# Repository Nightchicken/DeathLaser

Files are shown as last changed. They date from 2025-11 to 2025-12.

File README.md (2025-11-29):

# 🧠 ESP32 Project – ESP32 

## 👥 Team Members
| Name | Role | Contribution Summary |
|---|---|---|
| Bryon Cobb | | [Describe what they did briefly] |
| Matthew Kabat | | [Describe what they did briefly] |
| Joel Bowman | | [Describe what they did briefly] |
| Jett Moericke | | [Describe what they did briefly] |
| Steven Yang | | [Describe what they did briefly] |

1. Camera reading
2. Servo movement and limits
3. Laser on/off
4. Optional web based controller

Design and Fabrication of a Dual-Axis Servo Turret Mounts
Designed & Created by: Joel Bowman

1.	Motivation

The design of a dual-axis turret serves as a practical demonstration of the ESP-32 microcontroller’s capabilities. Although the ESP-32 is based on a RISC architecture with a reduced instruction set, it remains highly capable of generating precise pulse-width modulation (PWM) signals required for servo control. By integrating two MG995 servos, the system achieves motion along both the X and Y axes, enabling accurate positioning and tracking. When equipped with a camera, the turret can collect visual data and execute real-time tracking operations, showcasing the ESP-32’s ability to coordinate hardware and software tasks. This project therefore highlights not only the mechanical design and fabrication of servo mounts, but also the broader technical achievement of combining embedded control, signal modulation, and data-driven actuation in a cohesive system.
2.	Objectives

1.	To design, fabricate, and test servo brackets for MG995 servos enabling dual-axis rotation.          
2.	Mounts must securely hold the MG995 servos. 
3.	High strength is required to hold the weight extra attachments (Not breaking under use). 

3. Design Methodology and Materials 
•	CAD Modeling:
o	Tools used: Tinker CAD.
o	Designed plan: Breaking down the 
 
•	3D Printer Filament Material Selection:
o	PETG is chosen for durability, flexibility, and heat resistance compared to PLA.
o	While PETG is not as durable as TPU it is more ridged and easier to manufacture making it ideal material for mounting hardware.
o	PETG brand used and Specs:

4. Fabrication Process
3D Printing Setup
•	Printer Model: Creality Ender V3 SE
 
•	Nozzle Diameter: 0.2 mm
•	Layer Height: 0.2 mm
•	Infill Density: 45% (grid pattern)
•	Print Speed: 45 mm/s (optimized for PETG)
•	Material: PETG filament, selected for its higher impact resistance and thermal stability compared to PLA.
Observed Challenges:
•	PETG stringing due to insufficient retraction settings.
•	Bed adhesion difficulties requiring surface treatment.
•	Warping at bracket edges under prolonged print cycles.
•	Poor interlayer bonding at higher print speeds.
Assembly
•	Servo Mounting: MG995 servos were secured into the printed brackets using mechanical fasteners.
•	Fasteners: 1.4 × 12 mm screws, selected to reduce stress concentration and allow thicker bracket walls compared to larger bolts.
•	Wiring: Standard jumper wires were used for prototyping, enabling rapid connection to the ESP-32 microcontroller.
5. System Integration
The turret employs a dual-axis configuration:
•	Bottom Servo (Yaw): Provides rotation along the X-axis.
•	Top Servo (Pitch): Mounted orthogonally to enable vertical rotation along the Y-axis.
Control Architecture:
•	The ESP-32 generates PWM signals to modulate servo position.
•	Signals are routed through the servo driver circuitry.
•	Mechanical motion is achieved via the coupled servo brackets.

6. Challenges Encountered
•	Bracket Dimensions and Fitment: Initial bracket iterations obstructed servo insertion due to interference with structural features. Other designs were too thin, resulting in cracking under load when using 4 × 12 mm bolts. Transitioning to 1.4 × 12 mm screws allowed thicker bracket walls and improved rigidity.
o	Solution: Increased infill to 100% and introduced pilot holes using a 1/64 in drill bit. Simplified bracket geometry reduced stress concentrations and improved both print quality and mechanical strength.
•	Layer Adhesion in PETG: PETG requires precise tuning to achieve strong interlayer bonding. At default slicer settings (70 mm/s), adhesion was poor, leading to fragile parts.
o	Solution: Research indicated optimal print speeds between 35–50 mm/s. Adjusting to 40 mm/s improved layer fusion and overall part durability without sacrificing print time efficiency.
Minor Printing Issues
•	Bed Adhesion: Improved using glue stick application and elevated bed temperatures.
•	Stringing: Mitigated through retraction tuning and nozzle temperature adjustments.
Mechanical Issues
•	Bracket Snapping: Occurred under torque loads with larger bolts. Switching to smaller screws reduced localized stress and enabled thicker bracket design.
•	Reinforcement Strategies: Implemented 8 perimeter wall loops and increased infill density to enhance load-bearing capacity.
7. Results & Testing
•	Turret Performance:
o	Range of motion achieved.
o	Stability underload.
o	No misalignments and major vibrations.
 
8. Conclusion
	Overall, the task was a success as the Ender V3 SE performed well. Showing that Knowledge about the material and tunning was the most important aspect. As most of the issues occurring were due to improper tunning or a design that was not optimal for the structural limitations of the PETG. 
9. References/Specs 

---

## 🧩 1. Project Overview
Briefly describe your ESP32 project — Our group has used an Esp-32 to monitor heat signatures with a Thermal camera and upon finding an acceptable targert moving multiple lazer pointer to engage the target

---

## 🧱 2. Block Diagram
Provide a high-level **block diagram** showing the system components and their interactions.

**Example Layout:**

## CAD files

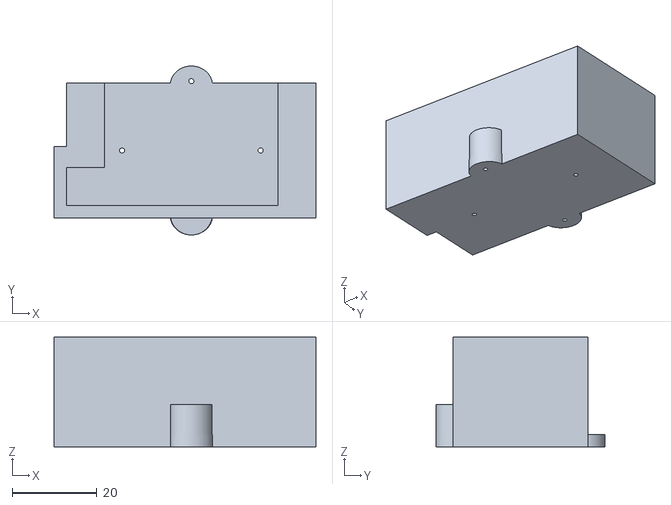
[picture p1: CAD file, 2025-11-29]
STL_Files/Top_servo_Mount_v8.stl
62.0 x 40.0 x 26.0

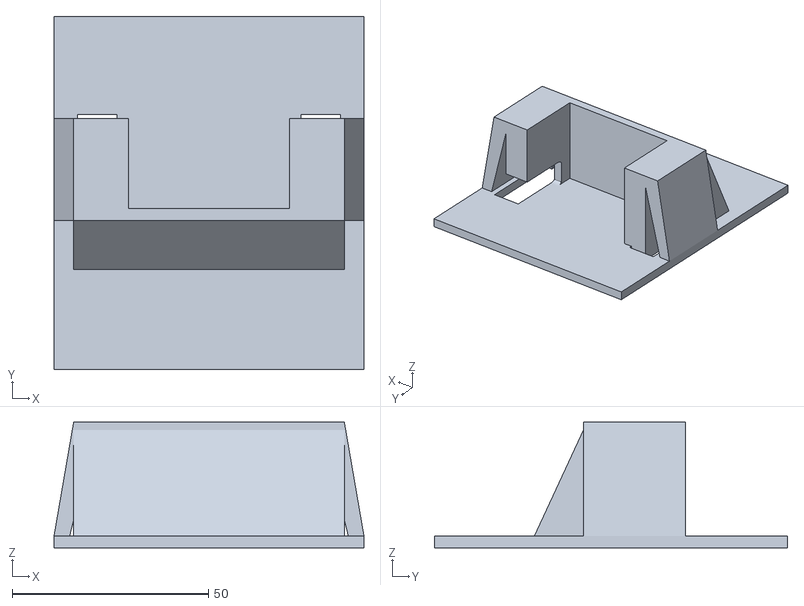
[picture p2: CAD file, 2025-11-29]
STL_Files/Turret Base V5 (1).stl
79.0 x 90.0 x 32.0

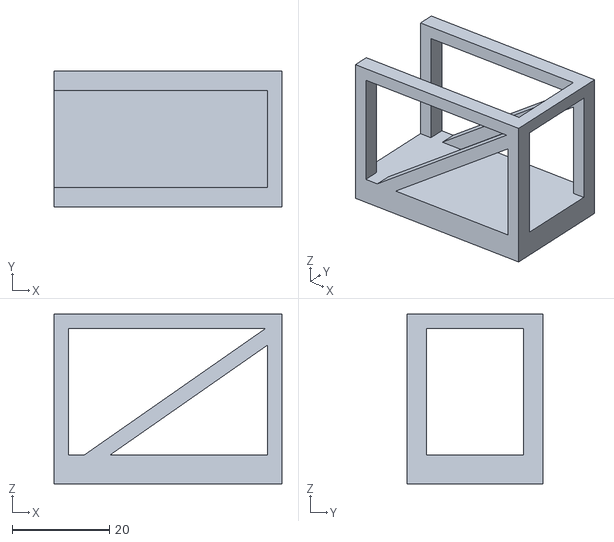
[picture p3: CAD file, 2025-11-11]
STL_Files/Turret Base V2-Skeleton.stl
47.0 x 28.0 x 35.0

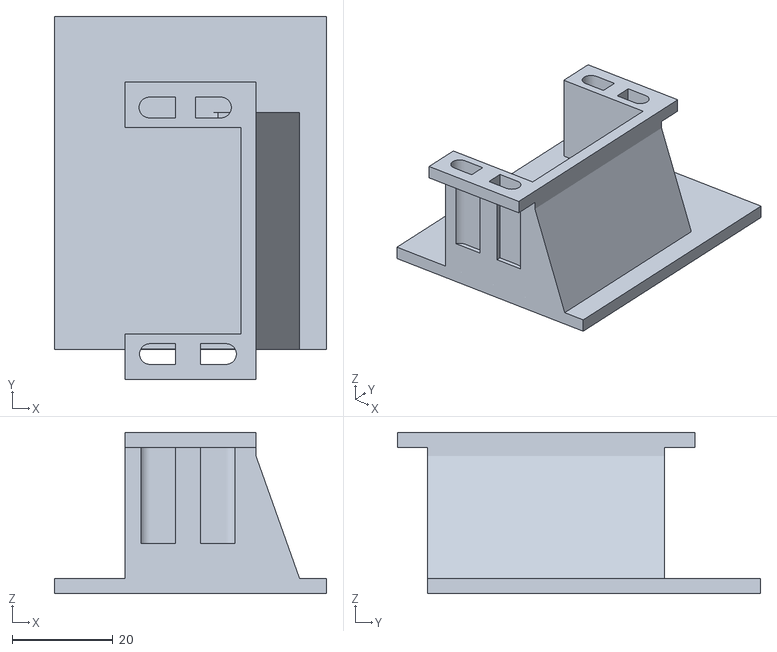
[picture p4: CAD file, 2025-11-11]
STL_Files/Turret Base V4.stl
54.0 x 72.0 x 32.0

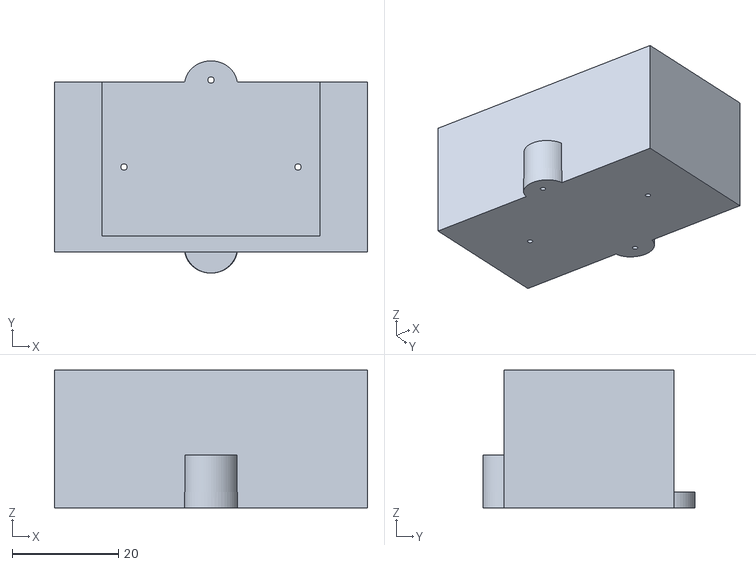
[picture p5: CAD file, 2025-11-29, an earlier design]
STL_Files/Top_servo_Mount_v7.stl
59.0 x 40.0 x 26.0

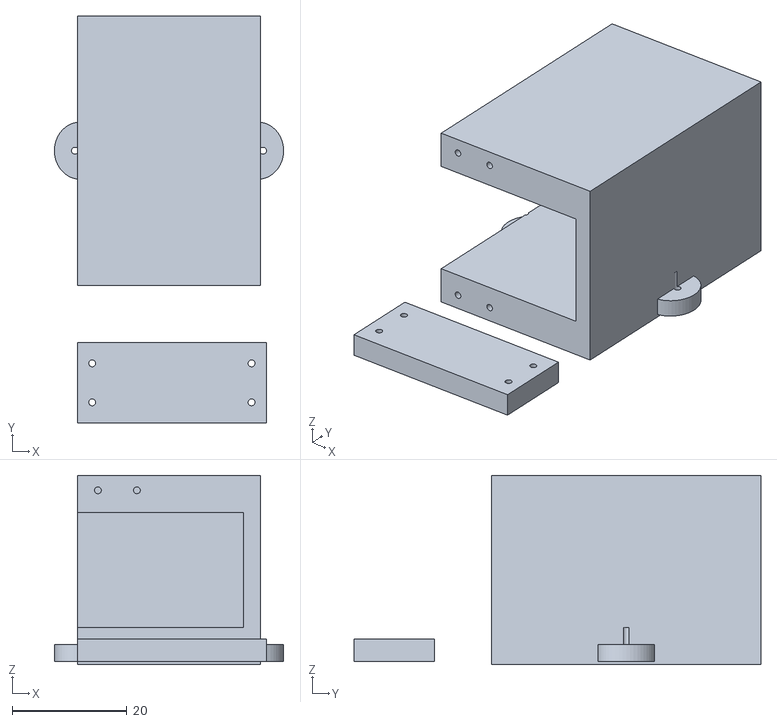
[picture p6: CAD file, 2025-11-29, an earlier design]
STL_Files/Top_servo_Mount_v6_5.stl
40.0 x 71.0 x 33.0

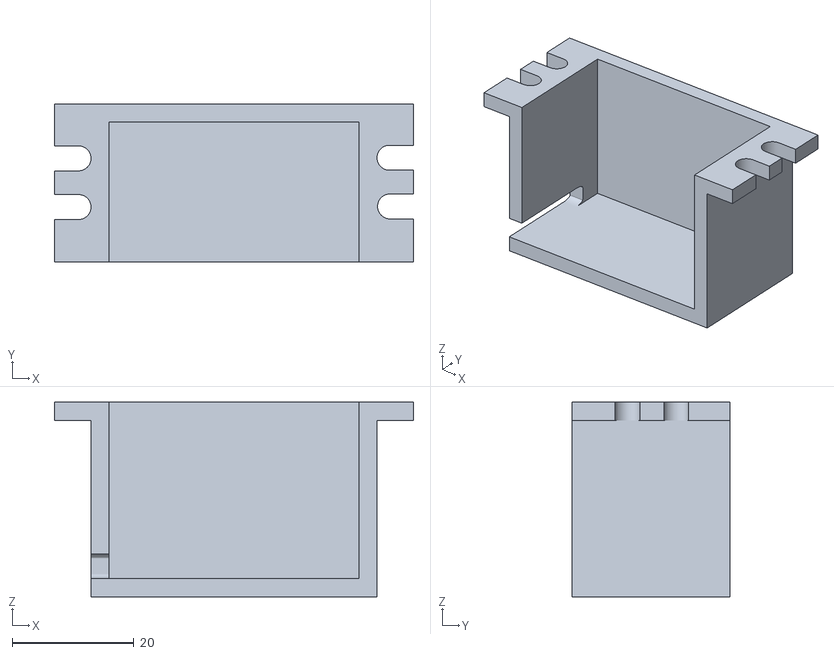
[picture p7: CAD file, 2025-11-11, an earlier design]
STL_Files/Turret Base V2_5.stl
59.0 x 26.0 x 32.0

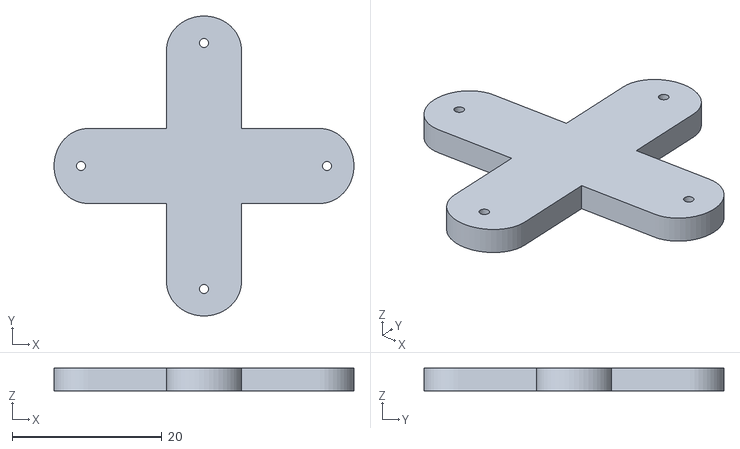
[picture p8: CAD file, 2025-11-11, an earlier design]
STL_Files/Top_servo_Mount_v1.stl
40.0 x 40.0 x 3.00

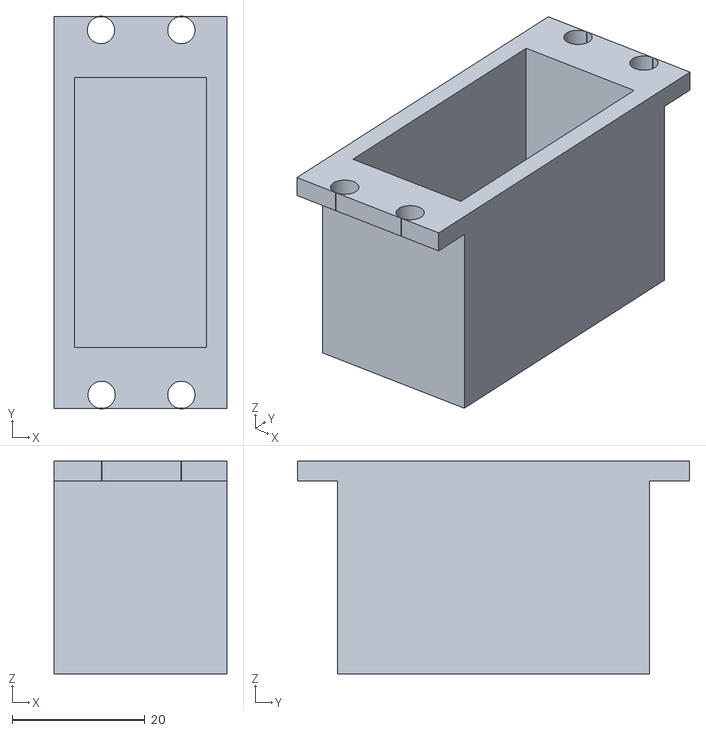
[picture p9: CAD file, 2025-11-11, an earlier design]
STL_Files/Turret Base V1.stl
26.0 x 59.0 x 32.0

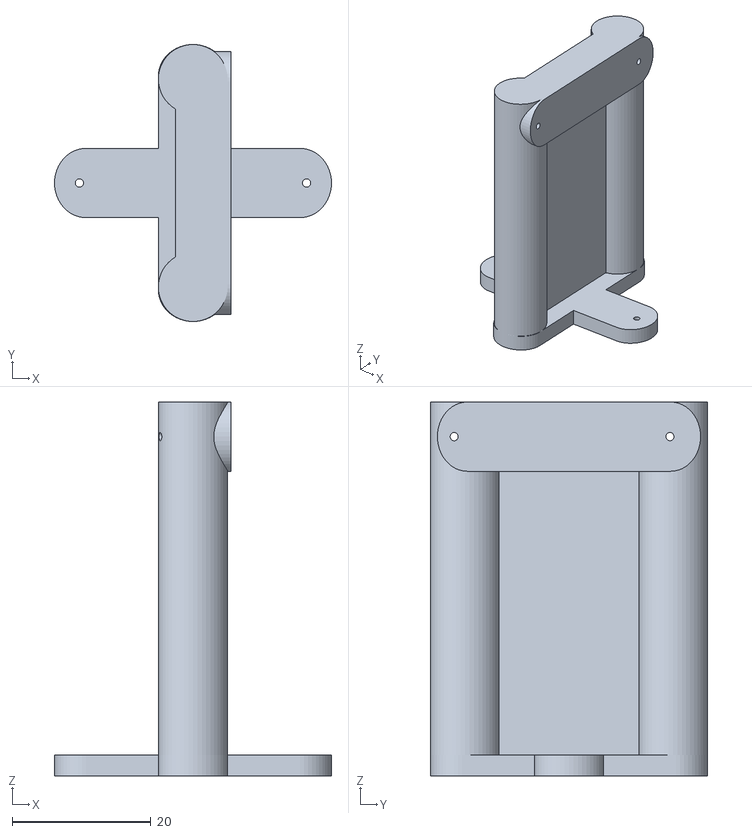
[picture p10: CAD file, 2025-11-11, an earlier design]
STL_Files/Top_servo_Mount_v2.stl
40.0 x 40.0 x 54.0

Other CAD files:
STL_Files/Turret Base V3.stl

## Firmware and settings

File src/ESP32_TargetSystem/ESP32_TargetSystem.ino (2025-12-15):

#include <Arduino.h>
#include "SystemInit.h"
#include "CameraController.h"
#include "LaserController.h"
#include "StorageManager.h"
#include "Patrol.h"

// ================================================================
// CONFIGURATION
// ================================================================
const int PAN_SERVO_PIN  = 25;
const int TILT_SERVO_PIN = 26;
const int SERIAL_BAUD    = 115200;

// ================================================================
// GLOBAL OBJECTS
// ================================================================
Patrol            patrol;            // Handles servo movement and pausing
LaserController   laserController;   // Handles laser firing logic
CameraController* cameraController = nullptr; // Singleton pointer
StorageManager* storageManager   = nullptr; // Singleton pointer

// ================================================================
// SETUP
// ================================================================
void setup() {
  // 1. Basic System Init
  SystemInit::beginSerial(SERIAL_BAUD);
  SystemInit::printBanner();

  // 2. Initialize Storage Singleton
  storageManager = StorageManager::getInstance();
  if (!storageManager->begin()) {
    Serial.println("[Error] SD Card failed or missing.");
  } else {
    storageManager->logEvent("System boot started.");
  }

  // 3. Initialize Patrol System
  // This automatically attaches servos and moves them to start position
  patrol.begin(PAN_SERVO_PIN, TILT_SERVO_PIN);
  Serial.println("[System] Patrol initialized.");

  // 4. Initialize Power & GPIO
  SystemInit::initGPIO();
  SystemInit::initCameraPower();

  // 5. Initialize Camera Singleton
  cameraController = CameraController::getInstance();
  if (!cameraController) {
    Serial.println("[CRITICAL] CameraController returned null!");
  }

  // 6. Initialize Laser Controller
  if (!laserController.begin()) {
    Serial.println("[Error] Laser controller init failed.");
  }

  if (storageManager) storageManager->logEvent("System setup complete.");
}

// ================================================================
// LOOP
// ================================================================
void loop() {
  // 1. UPDATE PATROL
  // This manages the servo movement AND the 5-second internal timer.
  patrol.update();

  // 2. CHECK LOCK STATE
  // If the patrol is "locked" (paused because we saw a target), 
  // we skip detection and just keep the signal active.
  if (patrol.isLocked()) {
    // Keep the laser ON to signal "I saw something"
    laserController.fireLaser(true); 
    
    // Exit loop early. We don't want to detect or save new photos 
    // while we are waiting for the 5-second timer to finish.
    return; 
  }

  // --- If we get here, we are actively searching ---

  // 3. LOOP RATE LIMITER
  // Camera reads are slow (~60ms), so we limit the loop speed to match.
  static unsigned long lastLoopMs = 0;
  unsigned long now = millis();
  if (now - lastLoopMs < 60) {
    return; 
  }
  lastLoopMs = now;

  // Safety Checks
  if (!cameraController || !storageManager) return;

  // 4. DETECT TARGET
  TargetInfo target = cameraController->captureAndDetectTarget(0.0f);
  
  // 5. DECISION LOGIC
  bool hasTarget = (target.confidence > 0.6f);

  if (hasTarget) {
    // --- TARGET ACQUIRED ---
    
    // A. Freeze the patrol (starts the 5-second timer inside Patrol class)
    patrol.onTargetFound();

    // B. Signal Immediately (Laser ON)
    laserController.fireLaser(true); 

    // C. Save Data & Thermal Photo (Happens once per detection event)
    storageManager->saveDetection(target.x, target.y, target.confidence);
    storageManager->saveThermalFrame(cameraController->getConstFrame(), 768);
    
    // Log it
    String logMsg = "Target Locked. Conf: " + String(target.confidence);
    storageManager->logEvent(logMsg);
    Serial.println(logMsg);

  } else {
    // --- NO TARGET ---
    // Ensure lasers are OFF while searching
    laserController.fireLaser(false);
  }
}

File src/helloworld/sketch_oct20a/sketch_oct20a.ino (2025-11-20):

#include <Arduino.h>
#include <Servo.h>

// ----- Servo Setup -----
Servo servo_bottom;
Servo servo_top;

// ----- Function Declaration -----
void patrol();

void setup() {
  servo_bottom.attach(9, 500, 2500);
  servo_top.attach(8, 500, 2500);

  Serial.begin(9600);
  Serial.println("Starting patrol...");
}

void loop() {
  patrol();
}

// ----- Function Definition -----
void patrol() {
  for (int bottomPos = 0; bottomPos <= 180; bottomPos += 20) {
    servo_bottom.write(bottomPos);
    delay(15);

    for (int topPos = 0; topPos <= 180; topPos++) {
      servo_top.write(topPos);
      delay(10);
    }
  }

  for (int bottomPos = 180; bottomPos >= 0; bottomPos -= 20) {
    servo_bottom.write(bottomPos);
    delay(15);

    for (int topPos = 0; topPos <= 180; topPos++) {
      servo_top.write(topPos);
      delay(10);
    }
  }
}

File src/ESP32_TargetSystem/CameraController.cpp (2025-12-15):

#include "CameraController.h" 
#include <Wire.h> 
#include <memory>
#include <fstream>
#include <Arduino.h> 

// >>>>>> SWITCHED TO ADAFRUIT LIBRARY <<<<<<
#include <Adafruit_MLX90640.h>

// Define the sensor object
static Adafruit_MLX90640 mlx; 

// =================================================================
// 1. STATIC MEMBER INITIALIZATION
// =================================================================
CameraController* CameraController::instancePtr = nullptr; 

// =================================================================
// 2. CONSTRUCTOR AND DESTRUCTOR
// =================================================================
CameraController::CameraController(){
    isConfigured = configureCamera();
    if (!isConfigured) {
        Serial.println("[Camera] Failed to configure camera.");
    } else {
        Serial.println("[Camera] Initialized.");
    }
}

CameraController::~CameraController(){
}

// =================================================================
// 3. SINGLETON GETTER
// =================================================================
CameraController* CameraController::getInstance(){
    if (instancePtr == nullptr){
        instancePtr = new CameraController(); 
    }
    return instancePtr;
}

// =================================================================
// 4. CORE CAMERA METHODS (Updated for Adafruit)
// =================================================================

bool CameraController::configureCamera(){
    // 1. Initialize I2C 
    Wire.begin(); 
    Wire.setClock(1000000); // 1 MHz clock for high FPS
    
    Serial.print("[Camera] Initializing MLX90640 (Adafruit Lib)...");
    
    // 2. Initialize Sensor (Adafruit uses begin() with address and Wire pointer)
    if (!mlx.begin(MLX90640_I2CADDR_DEFAULT, &Wire)) {
        Serial.println("FAILED. Check wiring!");
        isConfigured = false;
        return false;
    }
    
    // 3. Set Refresh Rate (Adafruit uses specific enums)
    mlx.setMode(MLX90640_CHESS); // 'Chess' mode is generally better for accuracy
    mlx.setResolution(MLX90640_ADC_18BIT);
    mlx.setRefreshRate(MLX90640_16_HZ);
    
    Serial.println("SUCCESS.");
    isConfigured = true;
    return true; 
}

float* CameraController::getFrame() {
    if (!isConfigured) {
        Serial.println("[Camera] ERROR: Sensor not configured. Returning default frame.");
        for (int i = 0; i < MLX_FRAME_SIZE; ++i) frame[i] = 20.0f; 
        return frame;
    }

    // Adafruit's getFrame takes the float array directly
    // It returns 0 on success
    if (mlx.getFrame(frame) != 0) {
        Serial.println("[Camera] ERROR: Read failed.");
        return frame; 
    }
    
    // Optional: Print center temp for debug
    // Serial.printf("[Camera] Frame captured. Center T: %.1f C\n", frame[12*32 + 16]);

    return frame;
}

const float* CameraController::getConstFrame() const {
    return frame;
}

void CameraController::testOutput(){
    Serial.println("[Camera] testOutput() stub running.");
}

// =================================================================
// 5. TARGET DETECTION (Unchanged)
// =================================================================
TargetInfo CameraController::captureAndDetectTarget(float desiredTemp){
    // 1. Capture a new frame
    float* currentFrame = getFrame();
    
    // 2. Normalization Setup
    float T_min = 999.0f; 
    float T_max = -999.0f; 
    
    // Find Min/Max
    for (int i = 0; i < MLX_FRAME_SIZE; ++i) {
        if (currentFrame[i] < T_min) T_min = currentFrame[i];
        if (currentFrame[i] > T_max) T_max = currentFrame[i];
    }
    
    float T_range = T_max - T_min;
    if (T_range < 0.1f) T_range = 1.0f; // Prevent div by zero

    // 3. Find Max Contrast
    float normalized_detection_threshold = 0.6f; 
    float max_normalized_value = 0.0f;
    int hotIndex = -1;

    for (int i = 0; i < MLX_FRAME_SIZE; ++i) {
        float T_normalized = (currentFrame[i] - T_min) / T_range; 
        
        if (T_normalized > max_normalized_value) {
            max_normalized_value = T_normalized;
            hotIndex = i;
        }
    }

    // 4. Initialize target 
    struct TargetInfo target = {0, 0, 0.0f};

    // 5. Set target if threshold met
    if (max_normalized_value > normalized_detection_threshold) {
        target.x = hotIndex % MLX_PIXEL_COLS;  
        target.y = hotIndex / MLX_PIXEL_COLS;  
        target.confidence = constrain(max_normalized_value, 0.0f, 1.0f); 
    }
    
    Serial.printf("[Camera] Min:%.1f Max:%.1f Conf:%.2f @ (%d, %d)\n", 
                  T_min, T_max, target.confidence, target.x, target.y);

    return target;
}

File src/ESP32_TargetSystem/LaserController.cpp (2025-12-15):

#include "LaserController.h"

// Constructor
LaserController::LaserController() 
  : initialized(false),
    laserPin(4)       // GPIO 4 for Laser (Check your wiring!)
{
    currentTarget = {0, 0, 0.0f};
}

bool LaserController::begin() {
    pinMode(laserPin, OUTPUT);
    digitalWrite(laserPin, LOW); // Ensure laser is OFF at startup

    initialized = true;
    Serial.println("[Laser] Controller initialized.");
    return true;
}

void LaserController::setTarget(const TargetInfo &target) {
    currentTarget = target;
}

// Update loop: Decides whether to pull the trigger
void LaserController::update(bool engage) {
    if (!initialized) return;

    if (engage && currentTarget.confidence > 0.6f) {
        // We are engaged and have a good target
        fireLaser(true);
    } else {
        // Safety: Always default to off
        fireLaser(false);
    }
}

// "aimAtTarget" removed because Patrol.cpp handles movement now.

void LaserController::fireLaser(bool on) {
    digitalWrite(laserPin, on ? HIGH : LOW);
}

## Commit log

2025-11-05 Implement servo patrol function in sketch
    Added servo control functionality to sweep two servos.
2025-11-11 Adding all my current STL files I used to help refine the MG995 servo mounts.
    [Top_servo_Mount_v1.stl, Top_servo_Mount_v2.stl, Turret Base V1.stl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]
2025-11-17 Boiler Plate code
    Basic file structure
2025-11-20 Boiler Plate
    THis is a basic template for completing the project
2025-11-24 Added rest of my stl files and updating read me to include documentation of the creation of the files.
    [Top_servo_Mount_v6_5.stl, Top_servo_Mount_v7.stl, Top_servo_Mount_v8.stl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]
2025-11-29 Ino file update
    This branch did 3 things. It changed the ino file to fit the camera controller cpp, created a base case for moving the servo motors, and also corrected a typo in the camera controller class such that the code could comp
    [CameraController.cpp, ESP32_TargetSystem.ino]
2025-12-02 Working Servo movement function
    This is a confirmed working Movement feature for the repo
2025-12-15 Final push
    This branch implements the following
    -Patrol files
    - save function
    - working camera
    -laser integration
